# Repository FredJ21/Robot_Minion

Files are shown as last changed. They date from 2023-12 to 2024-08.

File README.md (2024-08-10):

# Le Projet "ROBOT MINION"

***Introduction***

L'objectif de ce projet est de **concevoir** et **réaliser** un petit robot sympa, attractif, mignon, … un **MINION** 🤩 !!  

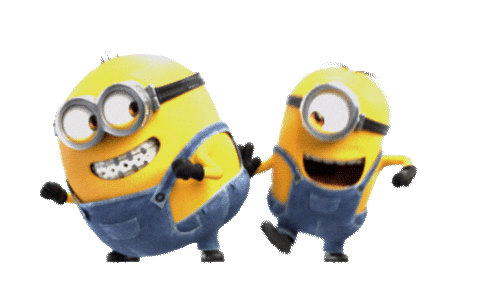
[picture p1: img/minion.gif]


Mais plus globalement, l’objectif de ce projet est de disposer d'**une base robotique** d’étude et de tests, simple, évolutive, et avec bien d'autres caractéristiques et fonctionnalités intéressantes :

* **Robustesse** , **solidité**
   * châssis en fibre de bois médium facile à modifier et réaliser (Découpe Laser). Il pourra également être réalisé en aluminium
   * pièces principales en impression 3D (en PLA ou PETG)

* **Modularité**
   * utilisation de profilés en aluminium 15x15 qui permettent de positionner les plateaux et des accessoires à la hauteur souhaitée
   * matrice de trous pré percés lors de la réalisation du châssis et des plateaux , permettant ainsi de positionner librement les différents éléments et évolutions
   * les pièces 3D disponibles pour éventuellement être modifiées, adaptées  (au format STL & Fusion360)

* **Espace**
   * 54 cm séparent le châssis inférieur et le bas bas du chapeau ,
   * les profilés alu verticaux sont espacés de 150 mm
   * ce qui donne un volume utile intérieur de 15 x 15 x 54 cm , mais certains éléments peuvent être positionnés sur l’extérieur (comme les bras, par exemple)

* **Puissance motrice**
   * motricité par l’utilisation de 2 moteurs CC à fort couple , qui pourront être remplacé par des modèles plus puissant si besoin

* **Programmation** et **connectivité**
   * Une carte Raspberry PI 4 au coeur du robot 🥳 !!! ( pouvant évoluer vers une version 5, bien entendu 😁 )
   * modules USB WiFi ou 4/5G
   * développement en Python (ou autre langage)
   * synthèse et reconnaissance vocal
   * traitement et tracking vidéo , computer vision

* **Evolutions**
   * on pourra greffer à souhait un certain nombre de capteurs, actionneurs, ou autres systèmes électroniques
   * **l’objectif est bien évidemment de faire évoluer** les éléments du robot , bras, tête, motricité …

Le robot, dans cette version, mesure environ 70 cm de haut, le chapeau supérieur et les plateaux ont un diamètre de 250 mm, l'empattement des roues avant/arrière est d’environ 300 mm.

🤔 La ressemblance est toute relative, mais il y a bien un petit aire de famille !!! 😜

<table  width="100%"><tbody>
<tr>
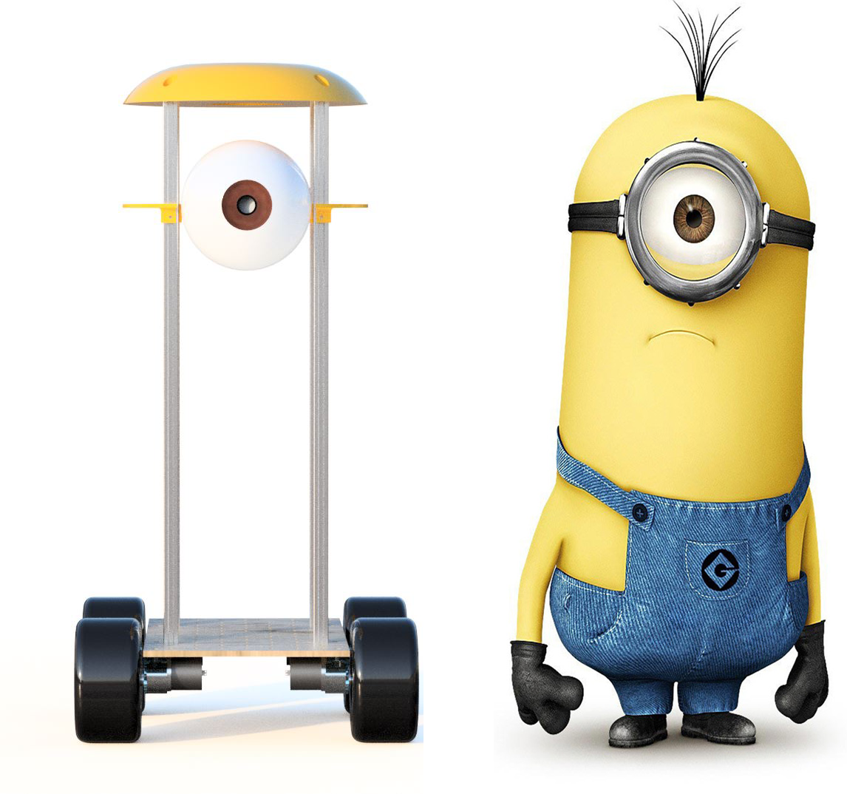
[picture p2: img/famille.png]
<td align="center" width="50%"></td>
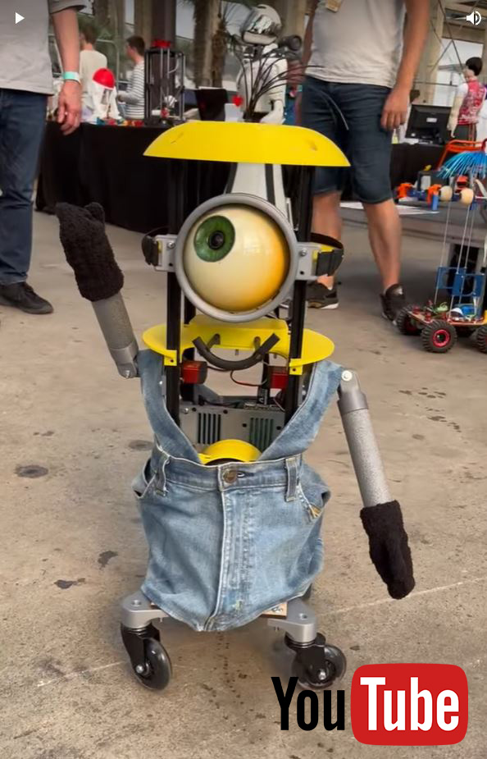
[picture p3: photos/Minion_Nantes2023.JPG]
<td align="center" width="30%">https://youtube.com/shorts/Kb3ByDOdsDA</td>

</tr>
</tbody></table>   

### Sommaire
* Les pièces réalisées en impression 3D
* Les autres pièces
* L'oeil
* La bouche
* Le mécanisme de l'épaule
* Le support de batterie
* L'électronique de commande
* Présentation du projet lors de l'ApéroBot 0x90 - le 11 octobre 2023
* Le projet MINION au JT de France 3 Pays De La Loire

---

## Les pièces réalisées en impression 3D

<table  width="100%"><tbody>
<tr>
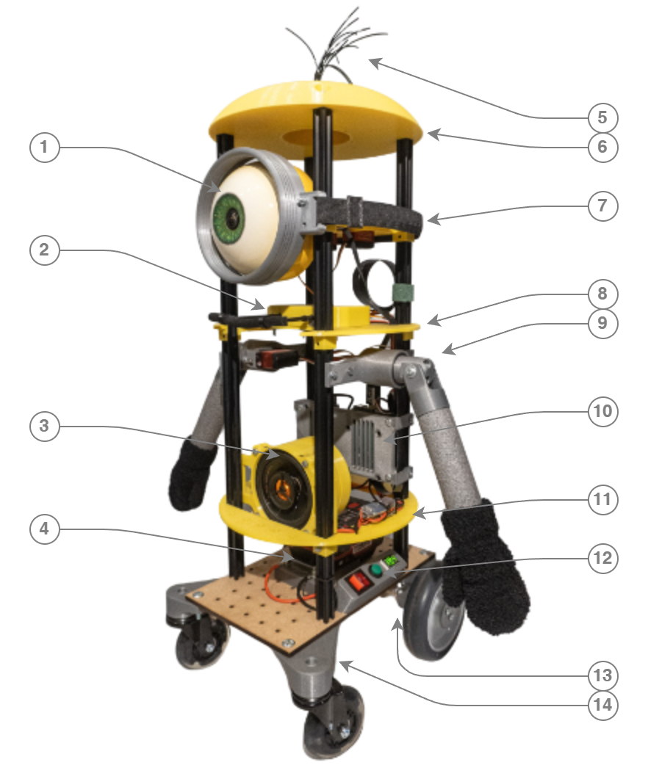
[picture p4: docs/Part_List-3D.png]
   <td width="60%"></td>
   <td align="left">
   (1) - L'<strong>oeil</strong> (voir plus bas) et la <a href="3D_STL/Lunette.stl">lunette</a><br>
   (2) - La <strong>bouche</strong> (voir plus bas)<br>
   (3) - <a href="3D_STL/HP_box.stl">Support du haut parleur</a><br>
   (4) - <strong>Batterie</strong> et sa base d'acceuil (voir plus bas)<br>
   (5) - <strong>Cheveux</strong> avec quelques bouts de TPU<br>
   (6) - <a href="3D_STL/Chapeau.stl">Chapeau</a> & Couvercles<br>
   (7) - <a href="3D_STL/Plateau_oeil_v2.stl">Plateau_oeil</a><br>
   (8) - <a href="3D_STL/Plateau_2.stl">Plateau 2</a><br>
   (9) - L'<strong>épaule</strong> (voir plus bas)<br>
   (10) - <a href="3D_STL/Support_RPI.stl">Support Raspberry PI</a><br>
   (11) - <a href="3D_STL/Plateau_3.stl">Plateau 3</a><br>
   (12) - Boutons de commande sur <a href="3D_STL/Power_button.stl">support</a> <br>
   (13) - <a href="3D_STL/Support_D37.stl">Supports de moteur</a><br>
   (14) - Support de roues libres <a href="3D_STL/Support_Roue_Libre_R.stl">droite</a> et  <a href="3D_STL/Support_Roue_Libre_L.stl">gauche</a><br>
   <br><br>

   </td>
 </tr>
</tbody></table>

- Fichiers STL pour l'impression 3D --> [3D_STL](3D_STL)
- Fichiers sources, au format Fusion 360 --> [3D_Fusion360](3D_Fusion360)

---

## Les autres pièces

<table  width="100%"><tbody>
<tr>
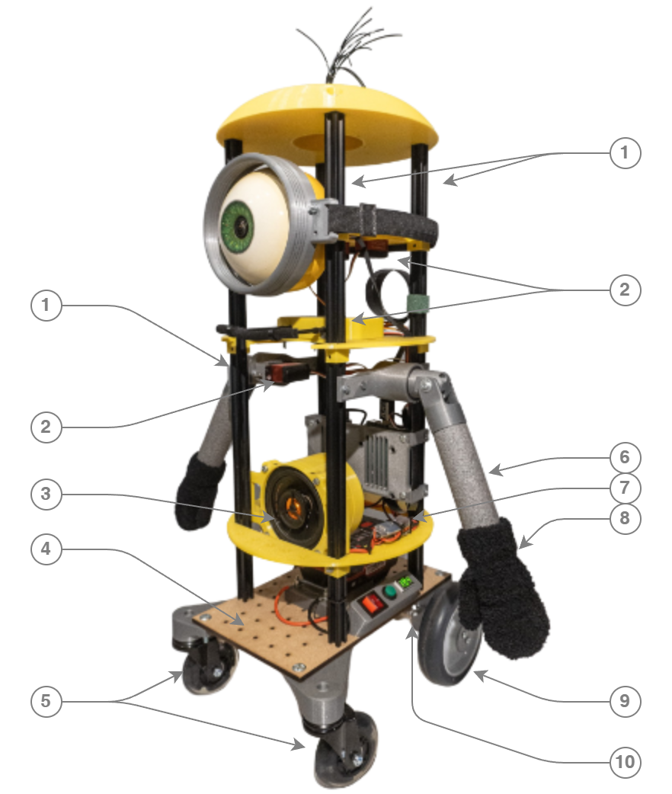
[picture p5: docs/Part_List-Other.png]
   <td width="60%"></td>
   <td align="left">
   (1) - <strong>4 profils</strong> en aluminium anodisé 1515 - 550mm de long <a href="https://fr.aliexpress.com/item/1005004071352633.html">aliexpress.com...</a><br>
   (2) - <strong>Servos moteurs</strong> numériques 30/35Kg.cm 180 degrés <a href="https://fr.aliexpress.com/item/32826867656.html">aliexpress.com...</a> <br>
   (3) - Haut-parleur 20 watts RMS (<a href="https://www.norauto.fr/p/haut-parleurs-norauto-sound-hp-100x-coaxial-2166455.html">norauto.fr...</a>) <br>
   (4) - <strong>Plateau</strong> de bois médium 6mm réalisé en découpe laser <a href="2D/Chassis_v4.svg">fichier svg</a> & dxf <br>
   (5) - <strong>Roulettes</strong> Luminescent Chaise Gamer <a href="https://www.amazon.fr/gp/product/B09N95T18G">amazon.fr...</a><br>
   (6) - <strong>Bras</strong> en mousse (d'isolation thermique en plomberie) diam 35mm <br>
   (7) - <strong>Regulateur</strong> UBEC 7A <a href="https://fr.aliexpress.com/item/32574612952.html">aliexpress.com...</a> <br>
   (8) - Petits gants pour les <strong>mains</strong> <a href="https://www.amazon.fr/gp/product/B0B7MNNZBG">amazon.fr...</a> <br>
   (9) - <strong>Roues</strong> dim 125mm <a href="https://www.leroymerlin.fr/produits/quincaillerie/quincaillerie-du-meuble/roue-et-roulette/roulette-de-meuble/roue-fixe-sur-axe-diam-125-mm-82629474.html">leroymerlin.fr...</a><br>
   (10) - <strong>Moteurs</strong> D37 CC à Brosses 12V 100 RPM 166 oz-in <a href="https://eu.robotshop.com/fr/products/12v-100rpm-166-oz-in-brushed-dc-motor">robotshop.com...</a><br>

   </td>
 </tr>
</tbody></table>

---

## L'oeil

L'oeil est réalisé en impression 3D avec poncage, peinture, et protection à la résine époxy. <br>
Il est articulé en X et Y autour d'un axe monté sur roulement.<br>
Il embarque une camera pour la carte Raspberry PI

***L'oeil est composé de plusieurs pièces :***

- la sphere de diamètre 130mm - <a href="3D_STL/Oeil_130.stl">Oeil_130.stl</a>
- un support pour la caméra - <a href="3D_STL/Oeil_Support_Cam.stl">Oeil_Support_Cam.stl</a>
- le support de l'oeil - <a href="3D_STL/Oeil_Support.stl">Oeil_Support.stl</a>
- l'axe - <a href="3D_STL/Oeil_Axe.stl">Oeil_Axe.stl</a>
- le raccordement au plateau - <a href="3D_STL/Oeil_Raccord_Plateau.stl">Oeil_Raccord_Plateau.stl</a>

<br>

- 3 roulements 608ZZ 8x22x7 <a href="https://www.amazon.fr/Roulements-Bearings-Skateboard-Longboard-Waveboard/dp/B07S3SZZST">amazon.fr...</a> <br>
- une camera RPI grand angle 175° <a href="https://fr.aliexpress.com/item/32881466491.html">aliexpress.com...</a> <br>
- <strong>2 Servos moteurs</strong> numériques 30/35Kg.cm 180 degrés <a href="https://fr.aliexpress.com/item/32826867656.html">aliexpress.com...</a> <br>

<table width="100%">
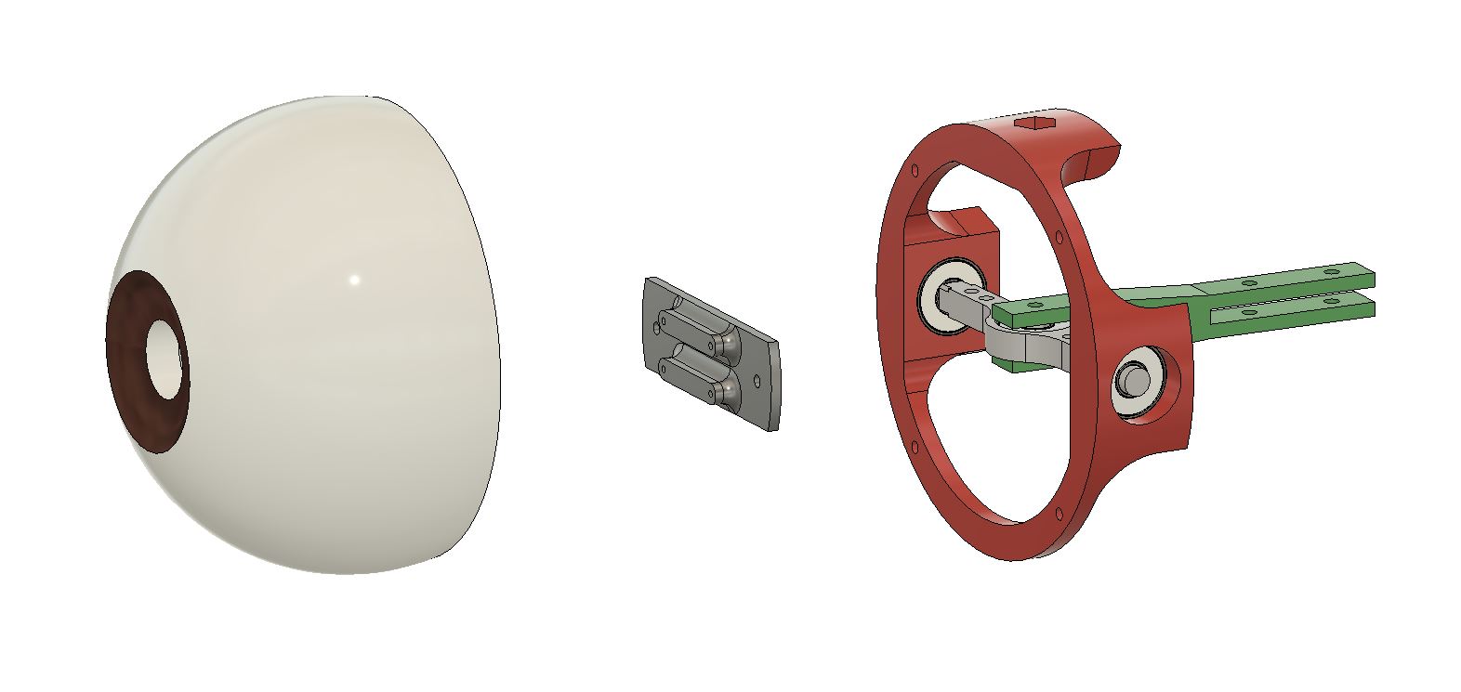
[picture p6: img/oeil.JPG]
<td align="center"></td>
</table>

- Piéces imprimées --> [3D_STL](3D_STL)
- Fichiers sources, au format Fusion 360 --> [3D_Fusion360](3D_Fusion360)

---
## La bouche

La bouche est réalisée avec 2 servos moteurs, quelques pièces imprimées, et un petit "boudin" de silicone

- Piéces imprimées
  - support pour les 2 moteurs --> [Bouche_1.stl](3D_STL/Bouche_1.stl)
  - 2 tiges --> [Bouche_2.stl](3D_STL/Bouche_2.stl)
  - le couvercle --> [Bouche_Couvercle.stl](Bouche_Couvercle.stl)
- Fichiers sources, au format Fusion 360 --> [3D_Fusion360](3D_Fusion360)

<table width="100%">
<td align="center">
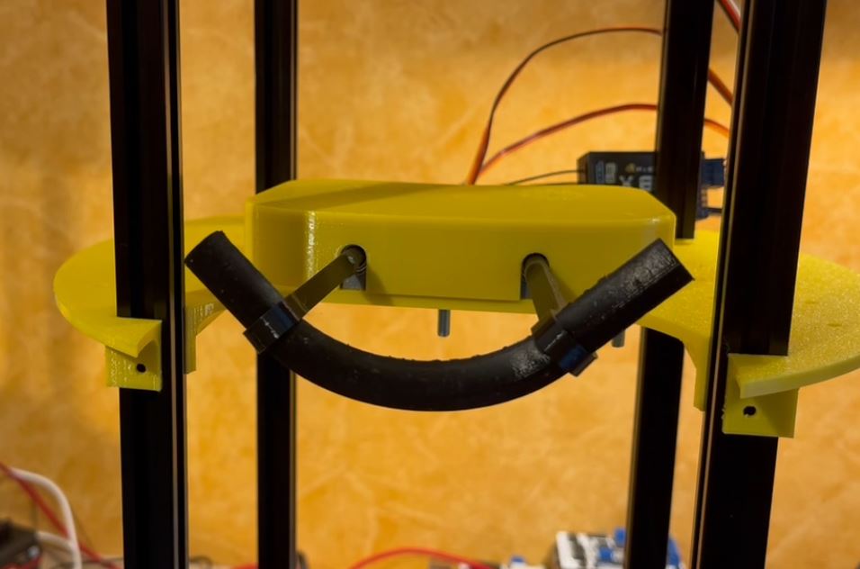
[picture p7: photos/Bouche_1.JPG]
 -
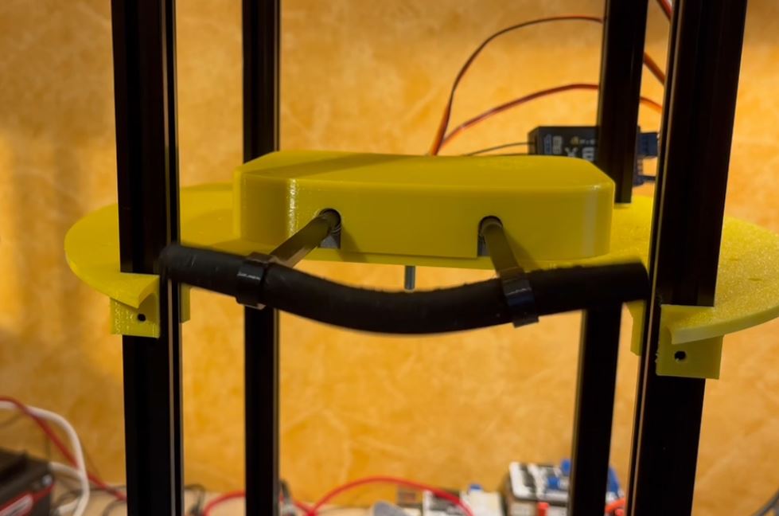
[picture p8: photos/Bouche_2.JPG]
 -
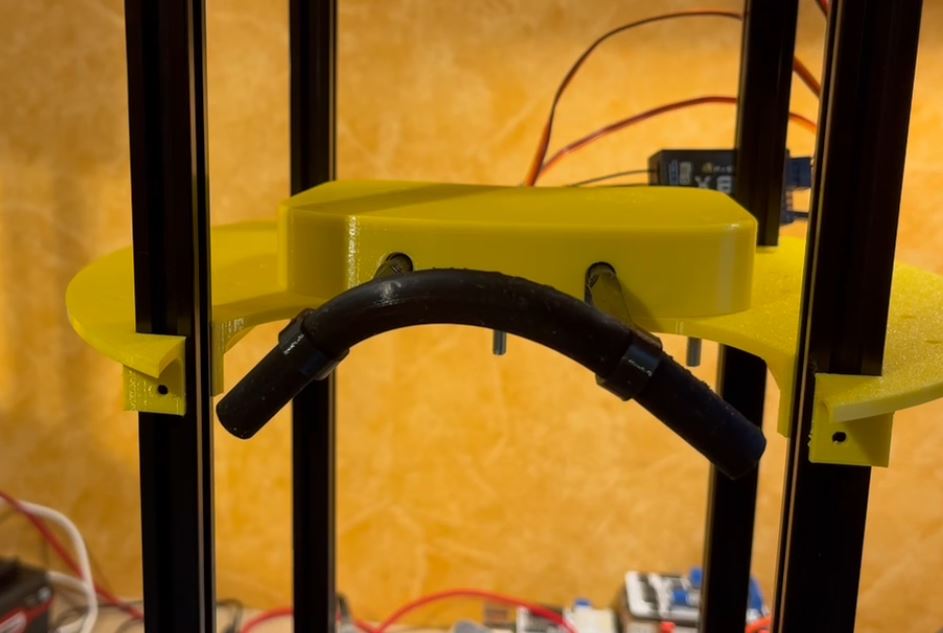
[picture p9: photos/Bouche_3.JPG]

</td>
</table>

---
## Le mécanisme de l'épaule

L'épaule est réalisée en impression 3D avec un servo moteur 30/35Kg et 2 roulements

- <strong>Servos moteurs</strong> numériques 30/35Kg.cm 180 degrés <a href="https://fr.aliexpress.com/item/32826867656.html">aliexpress.com...</a> <br>
- <strong>Roulements</strong> 30x37x4mm  <a href="https://www.amazon.fr/gp/product/B09SCMJTPJ/ref=ppx_yo_dt_b_search_asin_title">amazon.fr...</a> <br>
- 3 piéces imprimées --> [3D_STL](3D_STL)
- Fichiers sources, au format Fusion 360 --> [3D_Fusion360](3D_Fusion360)

<table width="100%">
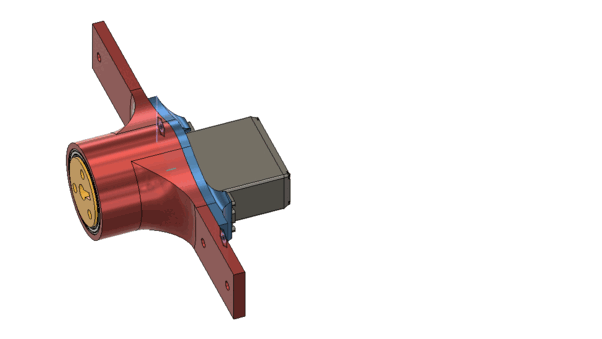
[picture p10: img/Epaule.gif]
<tr> <td align="center"> </td> </tr>
</table>

---

## Le support de batterie
***Liens & info*** :
- Batterie Parkside PAP 20 B3 - 20 V 4000mAh 80wh
- Chargeur Parkside PLG 20 C3
- petites lamelles en cuivre étamées ( réalisé avec un vieux tube de cuivre de plomberie )
- quelques vis M4

***Fichiers 3D*** :
- [Support_Batterie_up.stl](3D_STL/Support_Batterie_up.stl)
- [Support_Batterie_down.stl](3D_STL/Support_Batterie_down.stl)
- source : [Support_Batterie_Parkside.f3d](3D_Fusion360/)

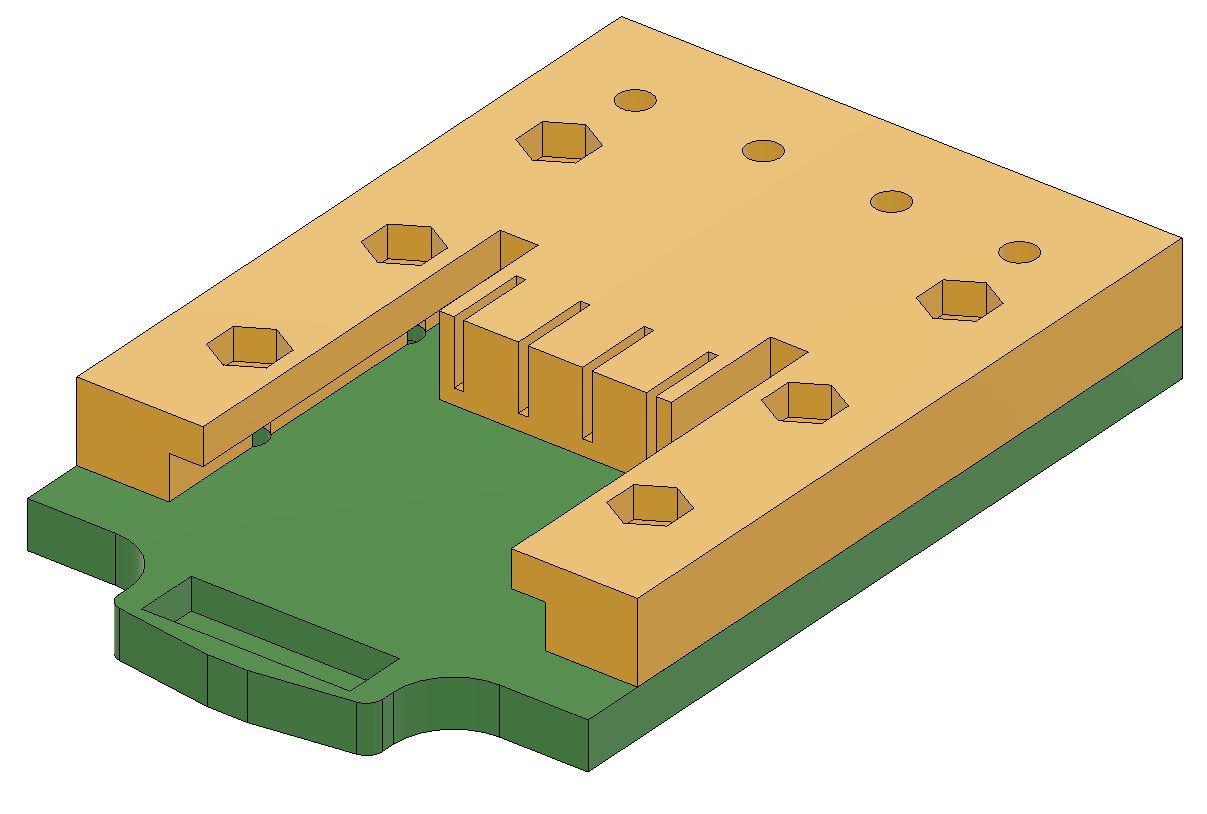
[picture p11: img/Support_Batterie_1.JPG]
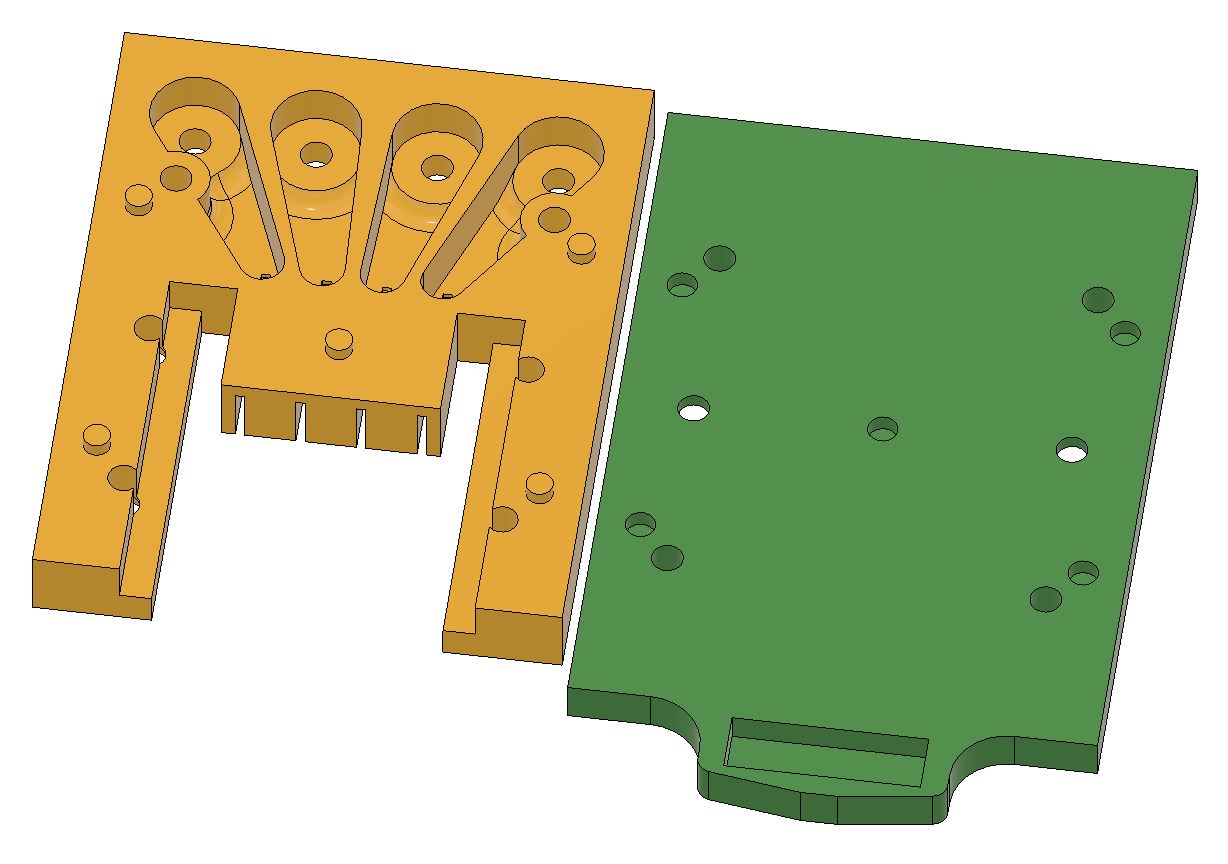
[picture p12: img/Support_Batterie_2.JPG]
| ||
|-----|-----|

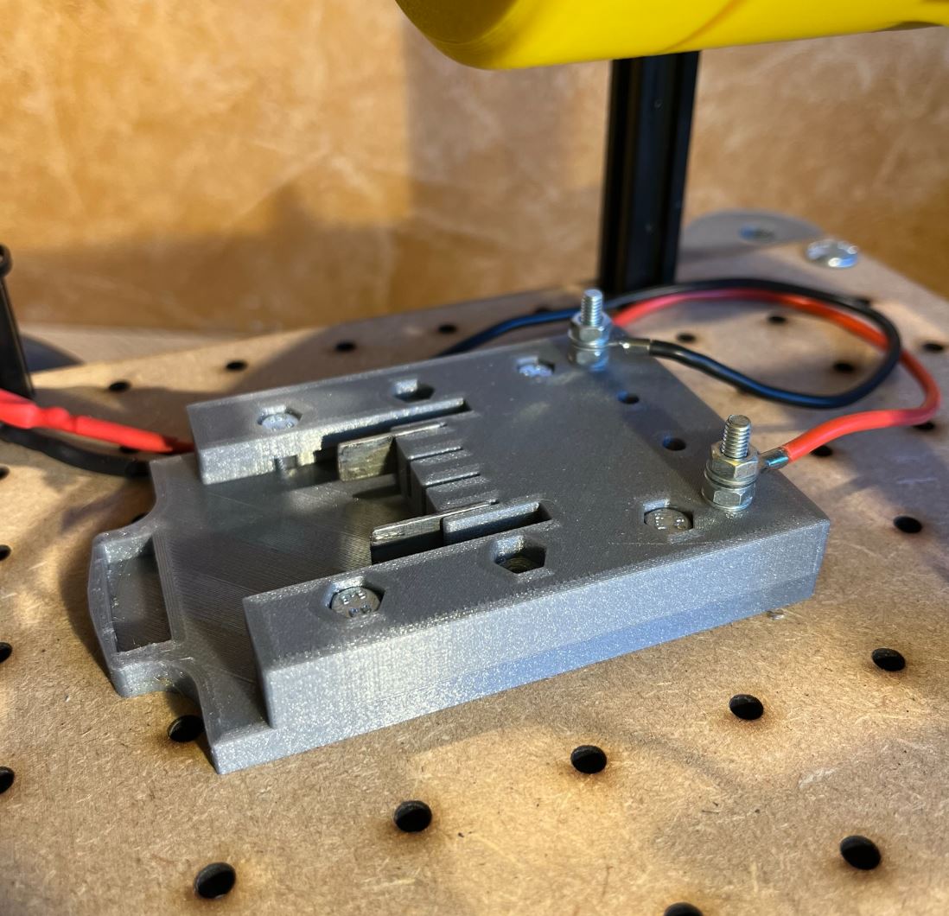
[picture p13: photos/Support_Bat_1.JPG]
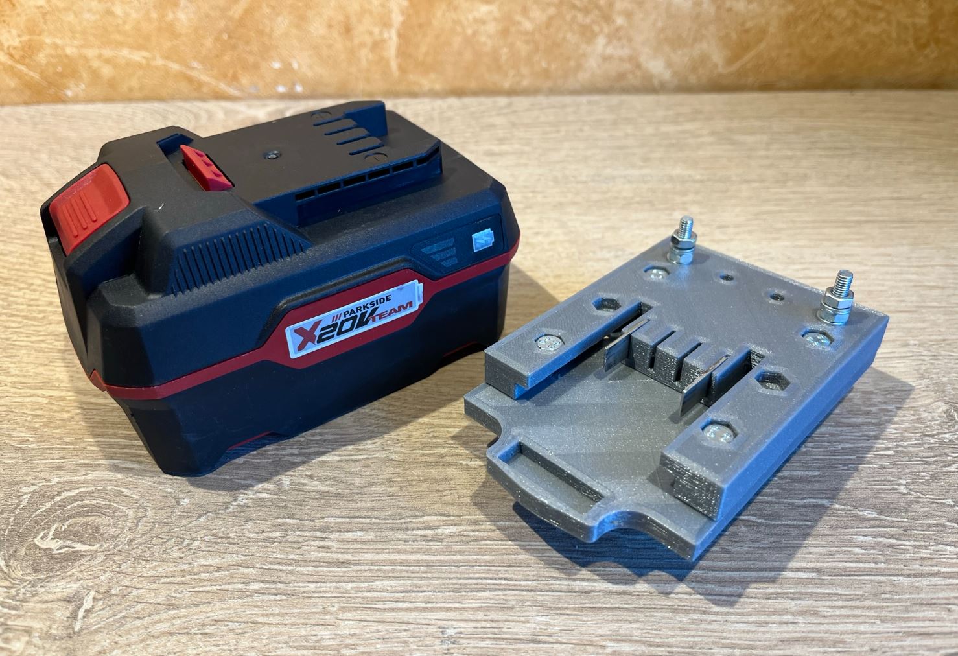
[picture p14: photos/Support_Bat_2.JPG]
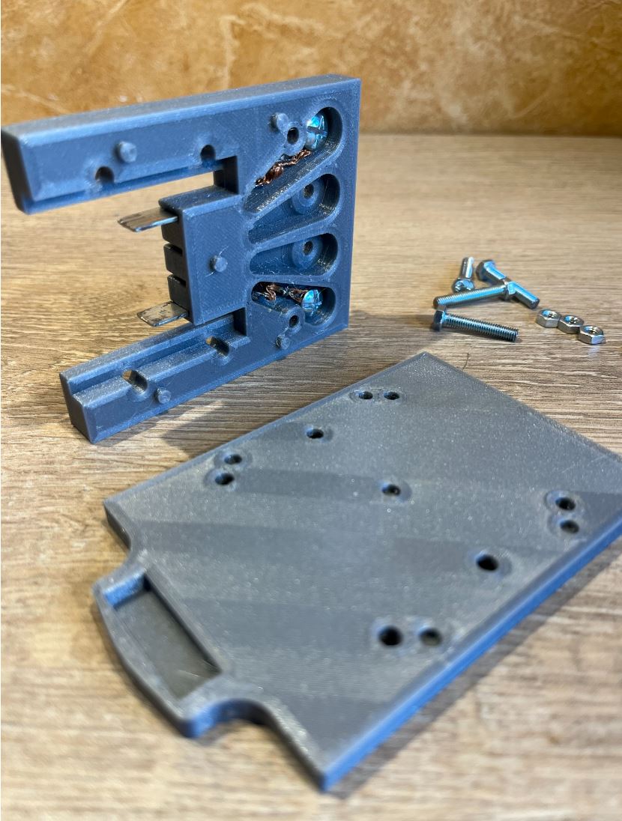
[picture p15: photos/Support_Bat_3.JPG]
|  |  |  |
|-----|-----|-----|

---

## L'électronique de commande

L'électronique embarquée est composée principalement :
- d'une carte Raspberry PI équipée d'une carte d'extension(*) (un HAT) pour la commande moteur https://github.com/FredJ21/Raspberry_PI_MotorDriverHat#readme
- d'un amplificateur audio
- d'un module WiFi USB
- de 2 regulateurs 5V afin séparer l'alimentation du RPI et des servos moteurs

***Important :*** Le projet peut également être réalisé sans cette carte d'extension "maison". Il suffira juste de choisir des drivers moteurs adaptés

<table  width="100%"><tbody>
<tr>
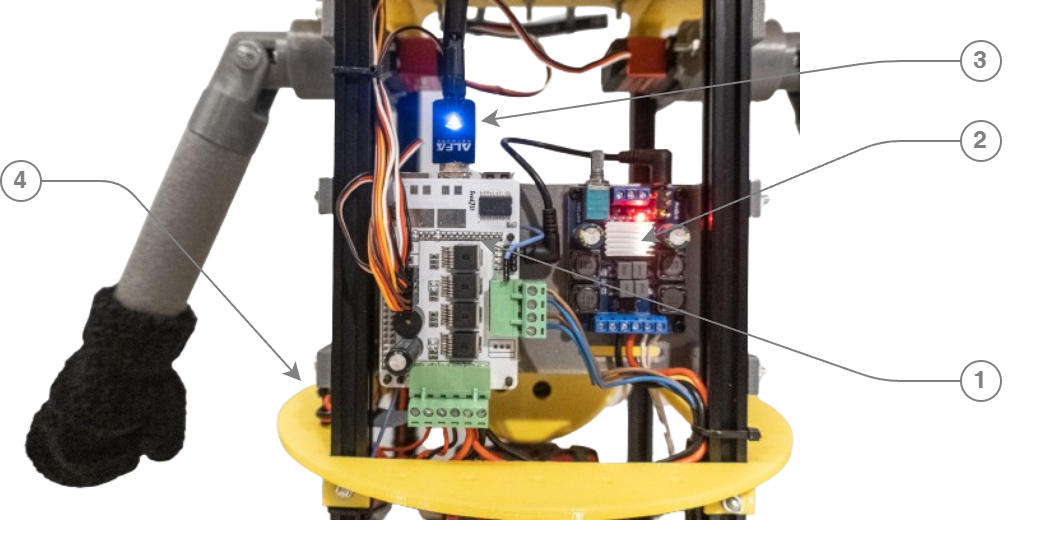
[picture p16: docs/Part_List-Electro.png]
   <td width="60%"></td>
   <td align="left">
   (1) - Une carte <strong>Raspberry PI</strong> 4 (ou 5 ! ) <a href="https://www.kubii.com/">www.kubii.com...</a><br>
   (2) - Une carte d'amplificateur numérique <a href="https://www.amazon.fr/gp/product/B09PL6R1L7">amazon.fr...</a> <br>
   (3) - Une carte WiFi USB (<a href="https://www.amazon.fr/gp/product/B0752CTSGD">amazon.fr...</a>) <br>
   (4) - <strong>2 Régulateurs</strong> UBEC 7A <a href="https://fr.aliexpress.com/item/32574612952.html">aliexpress.com...</a> <br>

   </td>
 </tr>
</tbody></table>

***Schéma global***

Schéma de principe avec la carte Raspberry PI, la carte d'extension (HAT drivers moteurs), et les éléments périphériques.

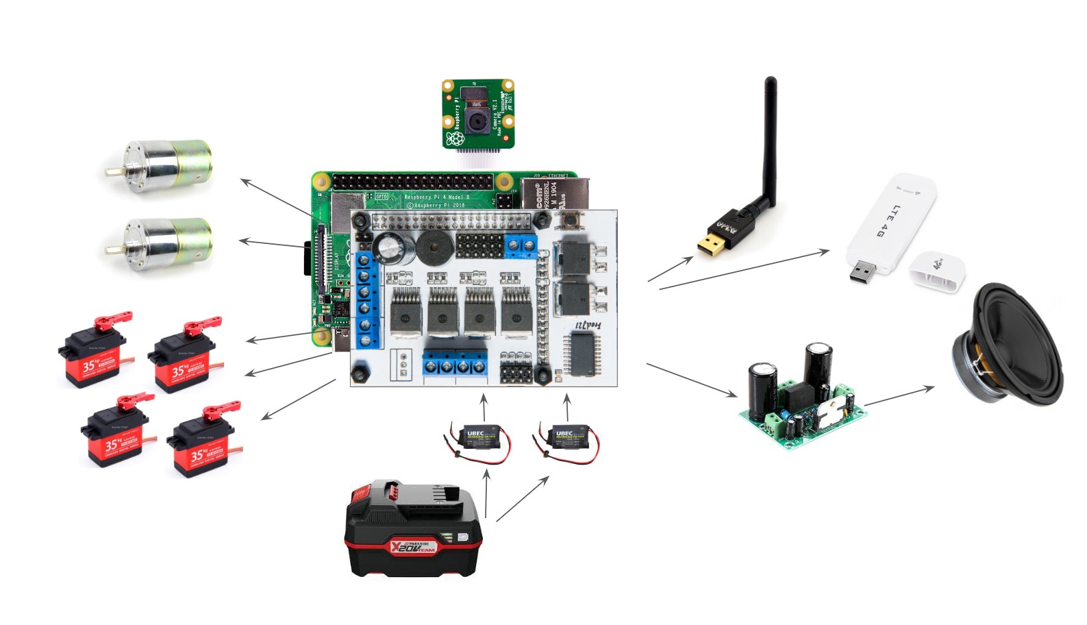
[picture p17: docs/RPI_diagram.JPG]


***Schéma de raccordement***

La carte d'extention permet de raccorder 3 alimentations distinctes :
- la tension directe de la batterie ~ 20V , pour l'alimentation des moteurs
- une tention régulée de 5V pour les servos moteurs
- une tention régulée de 5V pour la carte Raspberry PI

Les 2 moteurs CC ( pour le déplacement du robot ) sont raccordées à la carte d'extention
- GPIO 24 & 25 --> Mosfets moteur droit
- GPIO 26 & 27 --> Mosfets moteur gauche

Les servos moteurs sont raccordés aux sorties :
- GPIO 5 --> Oeil X
- GPIO 6 --> Oeil Y
- GPIO 12 --> Bras Droit
- GPIO 13 --> Bras Gauche
- GPIO 7 --> Bouche moteur Droit
- GPIO 8 --> Bouche moteur Gauche

De plus, la carte dispose d'autres GPIO libres , et de :
- GPIO 18 --> buzzer
- GPIO 19 --> Bouton poussoir

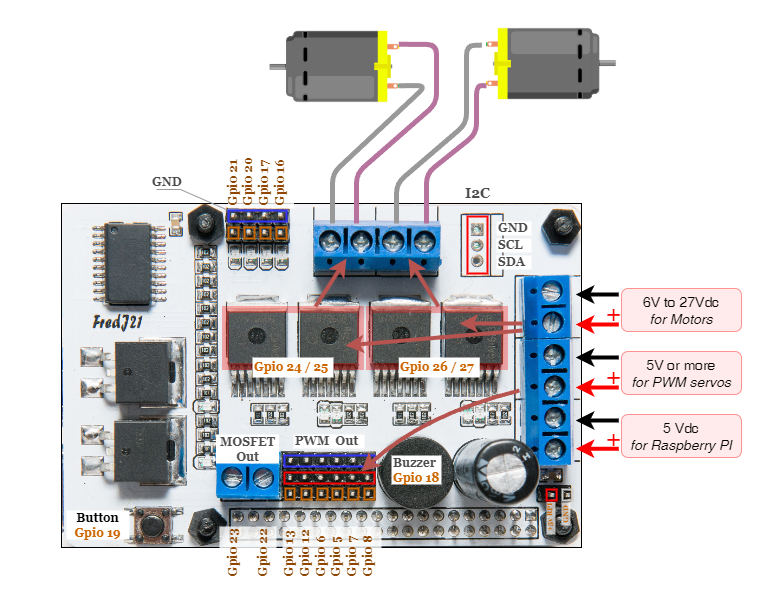
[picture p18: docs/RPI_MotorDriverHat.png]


***Raspberry PI - PinOut***

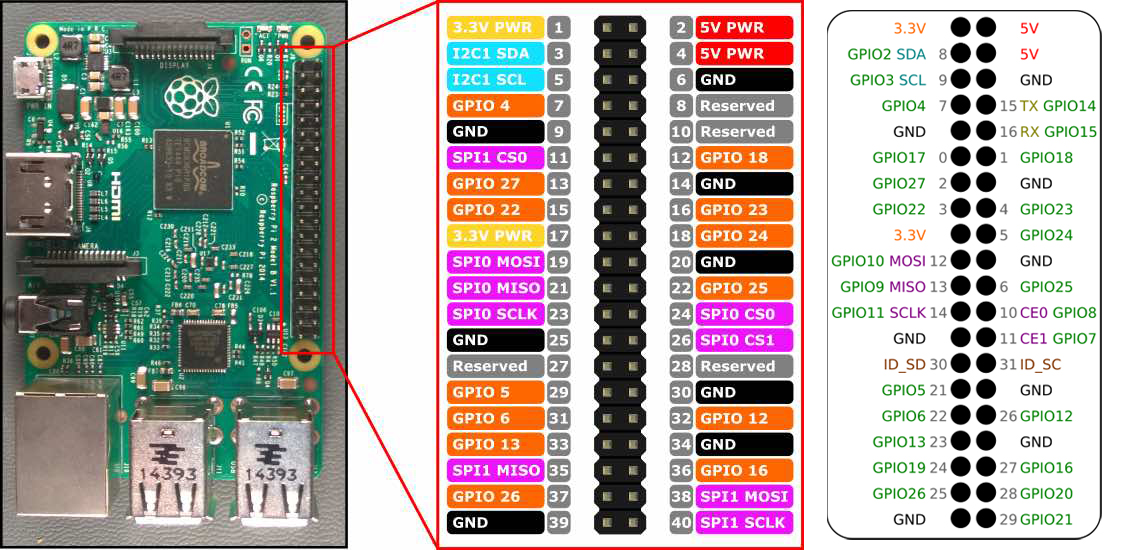
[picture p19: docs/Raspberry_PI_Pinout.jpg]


---

## Programmation

Le programme de gestion et son interface Web sont toujours en cours de développement ...
... mais je tente de stabliser et simplifier l'installation, ainsi que le packaging .... dans en autre Repos Git  :
( actuellement en cours de construction ) 

https://github.com/FredJ21/Robot_Minion_Dev

---

## Présentation du projet lors de l'ApéroBot 0x90 - le 11 octobre 2023
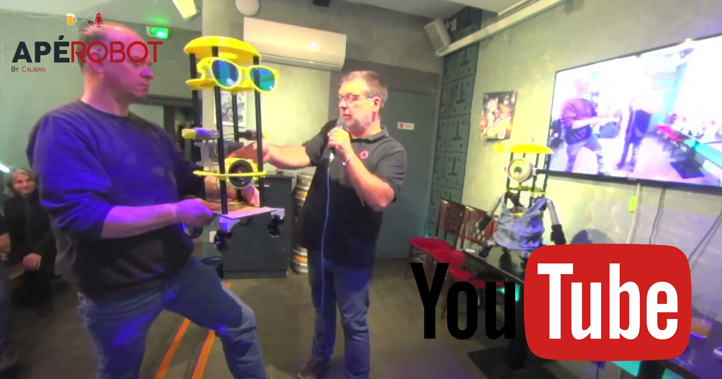
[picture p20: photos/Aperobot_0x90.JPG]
<br>
- https://youtu.be/tXXc-RWyAaM
- Slides de présentation: [202310_Caliban_Robot_MINION.pptx](https://docs.google.com/presentation/d/1i7fHR1yLxM-sZlLi-bkuZh3kFmp7REDd2zA3NFKi7cQ/)

---

## Le projet MINION au JT de France 3 Pays De La Loire
- JT du 7 Juillet 2023 - Nantes Maker Campus 2023

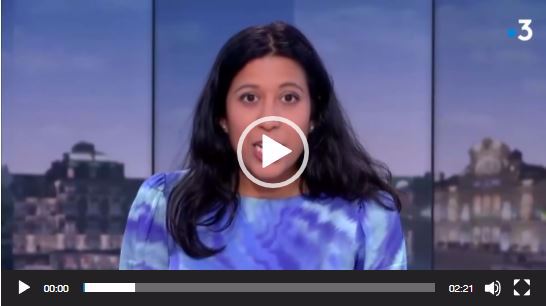
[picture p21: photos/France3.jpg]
<br>
- https://youtu.be/sHJWs27naQQ

---

### Authors
Frederic JELMONI<br>
https://www.youtube.com/@fred-robotic<br>
https://www.facebook.com/fredrobotic<br>

### MIT License
Permission is hereby granted, free of charge, to any person obtaining a copy
of this software and associated documentation files (the "Software"), to deal
in the Software without restriction, including without limitation the rights
to use, copy, modify, merge, publish, distribute, sublicense, and/or sell
copies of the Software, and to permit persons to whom the Software is
furnished to do so, subject to the following conditions:

The above copyright notice and this permission notice shall be included in all
copies or substantial portions of the Software.

THE SOFTWARE IS PROVIDED "AS IS", WITHOUT WARRANTY OF ANY KIND, EXPRESS OR
IMPLIED, INCLUDING BUT NOT LIMITED TO THE WARRANTIES OF MERCHANTABILITY,
FITNESS FOR A PARTICULAR PURPOSE AND NONINFRINGEMENT. IN NO EVENT SHALL THE
AUTHORS OR COPYRIGHT HOLDERS BE LIABLE FOR ANY CLAIM, DAMAGES OR OTHER
LIABILITY, WHETHER IN AN ACTION OF CONTRACT, TORT OR OTHERWISE, ARISING FROM,
OUT OF OR IN CONNECTION WITH THE SOFTWARE OR THE USE OR OTHER DEALINGS IN THE
SOFTWARE.

### Copyright
Copyright (c) 2023 Frederic JELMONI

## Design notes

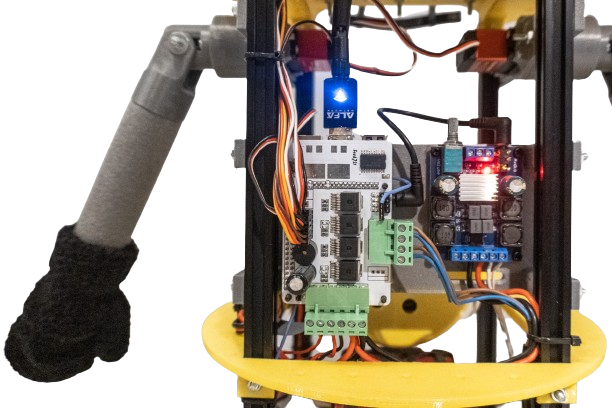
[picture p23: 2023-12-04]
docs/2023-12_Minion_2.png

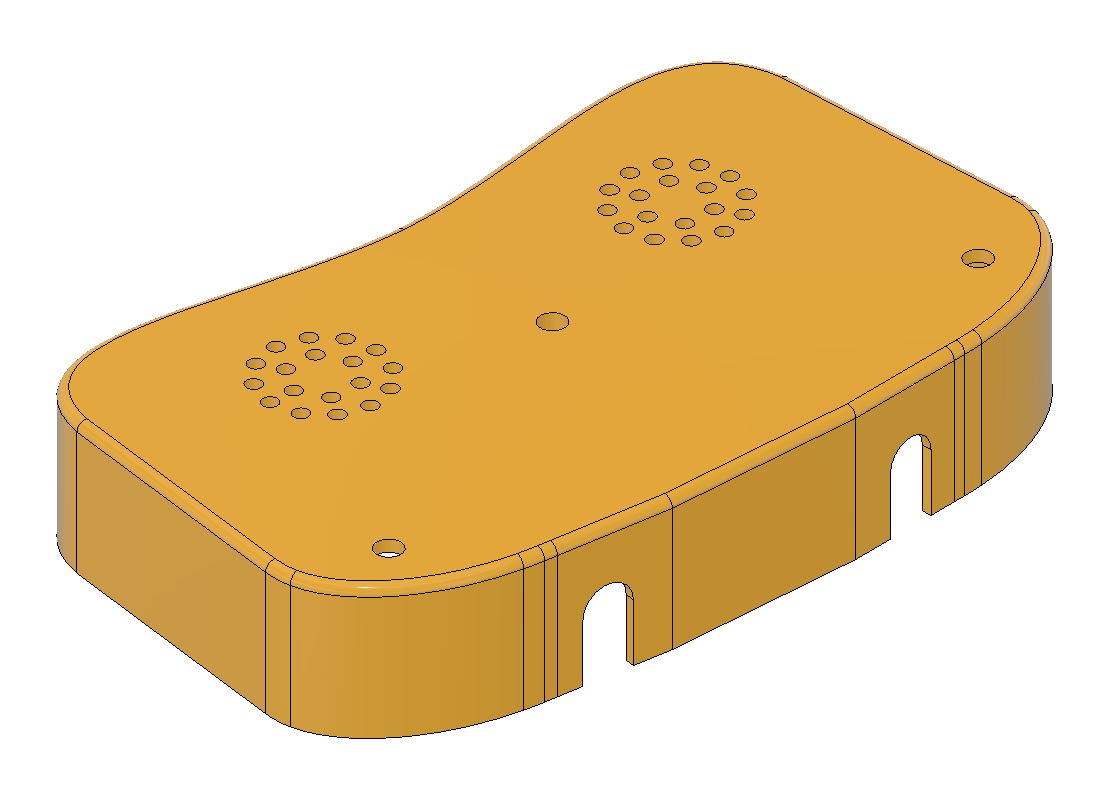
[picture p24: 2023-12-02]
img/bouche_couvercle.jpg

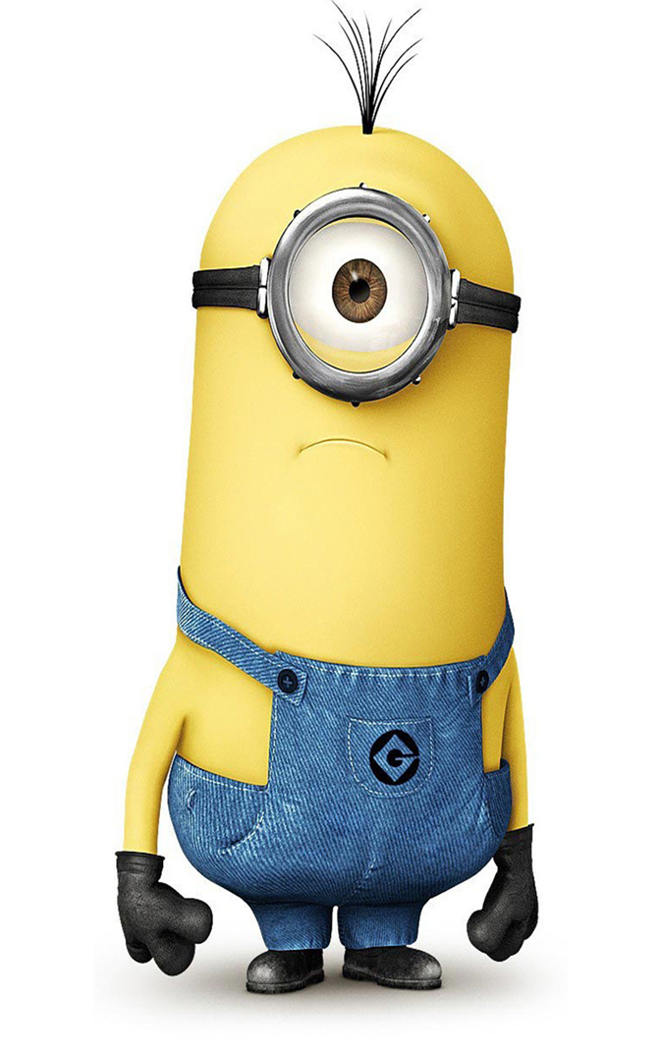
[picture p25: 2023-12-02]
img/mignon2.png

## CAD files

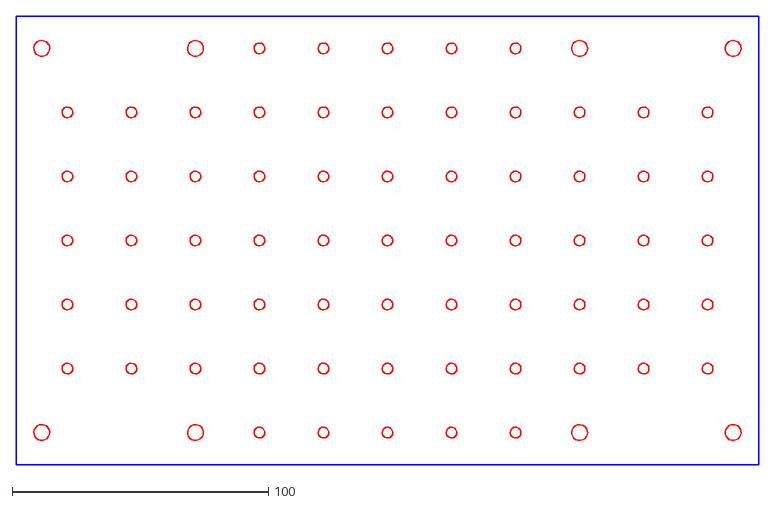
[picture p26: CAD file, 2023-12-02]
2D/Chassis_v4.dxf
290.0 x 175.0

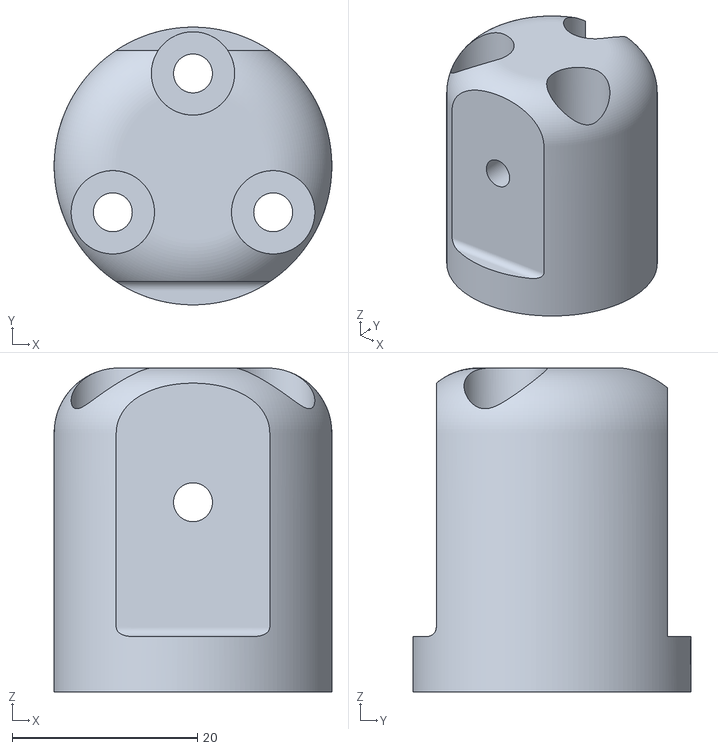
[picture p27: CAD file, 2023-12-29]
3D_STL/Epaule_4.stl
30.0 x 30.0 x 35.0

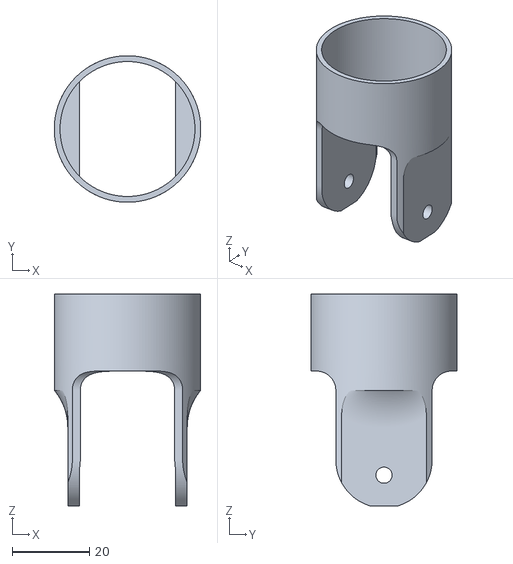
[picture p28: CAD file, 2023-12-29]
3D_STL/Epaule_5.stl
38.0 x 38.0 x 55.0

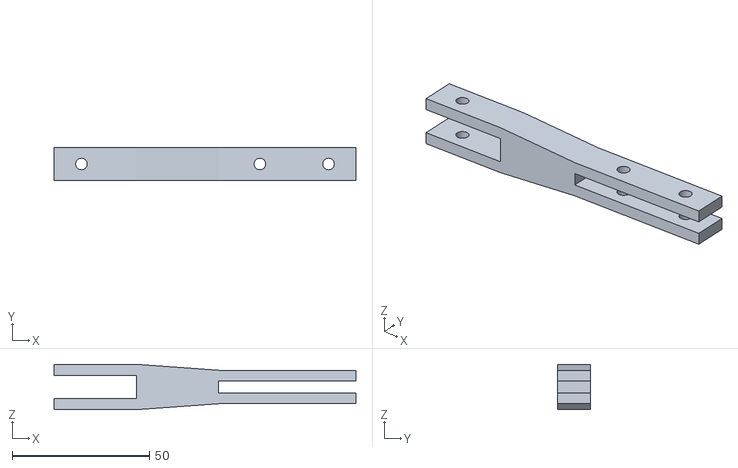
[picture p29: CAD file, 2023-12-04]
3D_STL/Oeil_Raccord_Plateau.stl
110.0 x 12.0 x 16.5

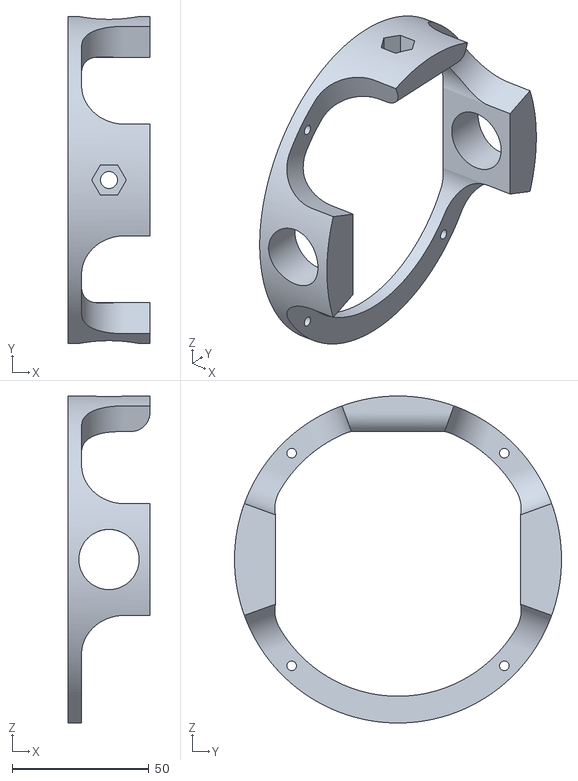
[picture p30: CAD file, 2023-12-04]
3D_STL/Oeil_Support.stl
30.0 x 119.6 x 119.6

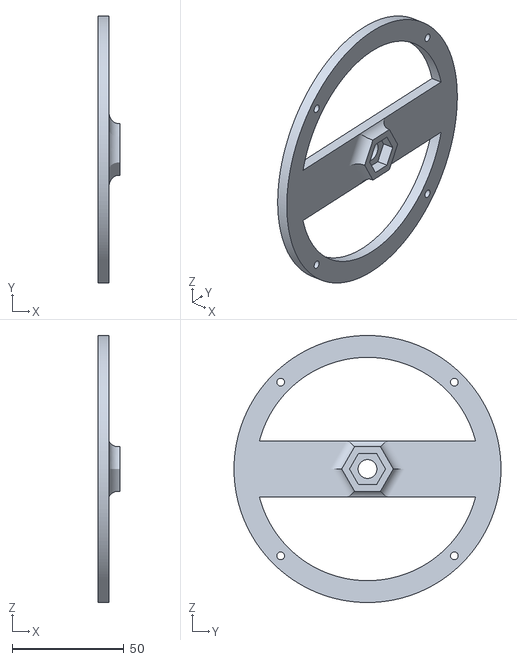
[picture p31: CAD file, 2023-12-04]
3D_STL/Oeil_Support_pour_peinture.stl
10.0 x 119.6 x 119.6

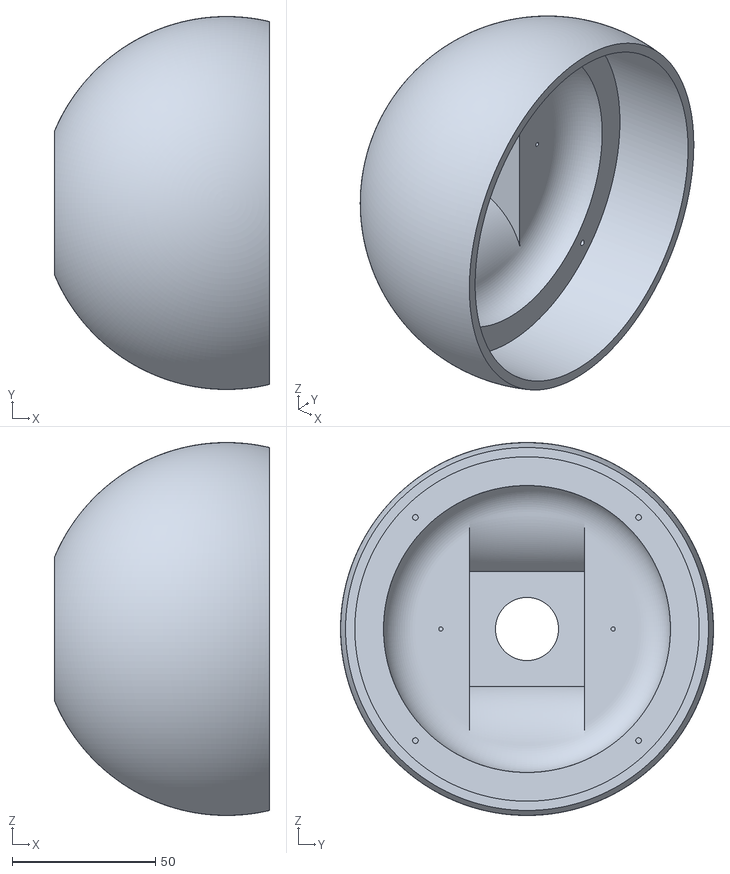
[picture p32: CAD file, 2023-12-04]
3D_STL/Oeil_130.stl
75.0 x 130.0 x 130.0

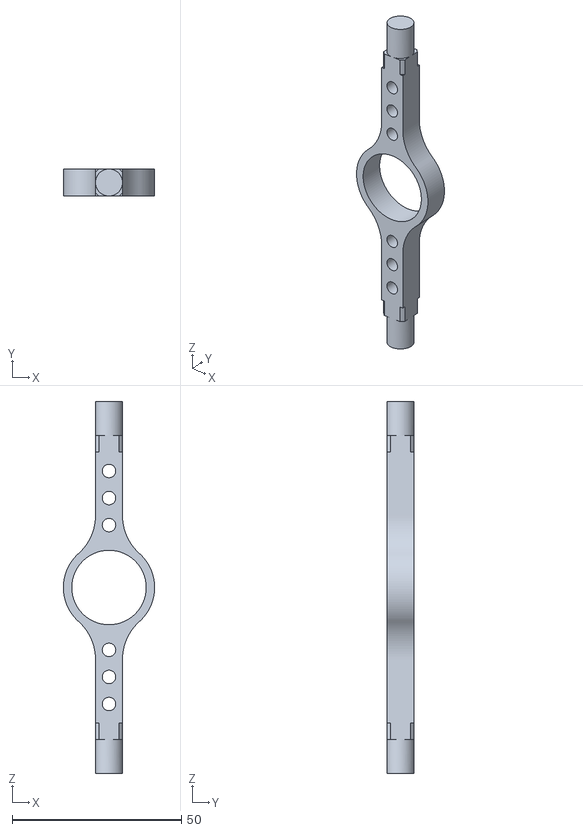
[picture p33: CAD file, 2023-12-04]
3D_STL/Oeil_Axe.stl
27.0 x 8.00 x 110.0

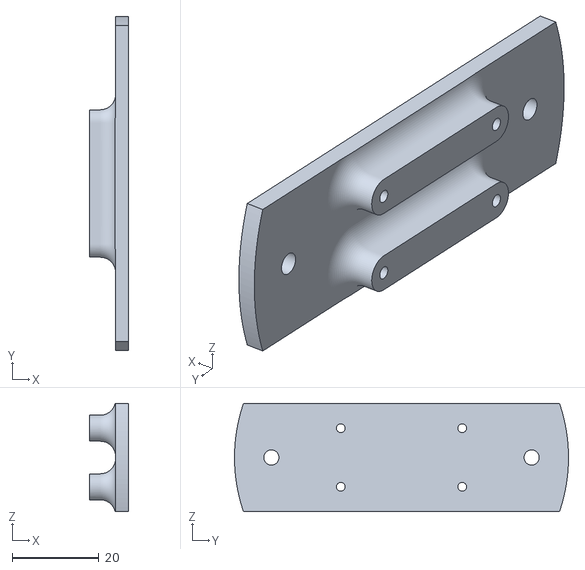
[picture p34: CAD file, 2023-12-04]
3D_STL/Oeil_Support_Cam.stl
9.00 x 77.0 x 25.0

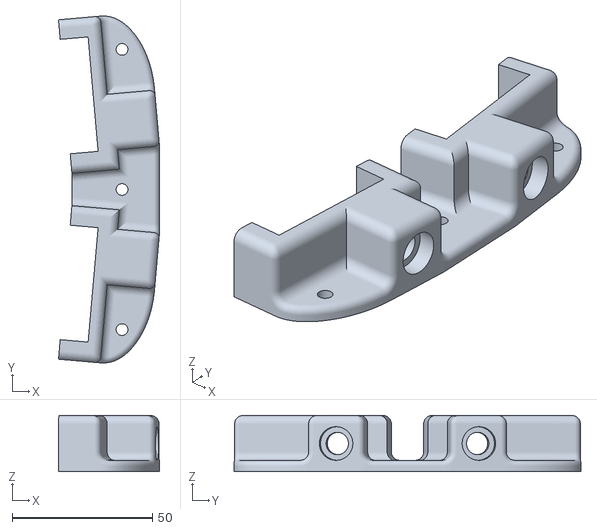
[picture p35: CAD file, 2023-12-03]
3D_STL/Bouche_1.stl
36.1 x 123.8 x 20.0

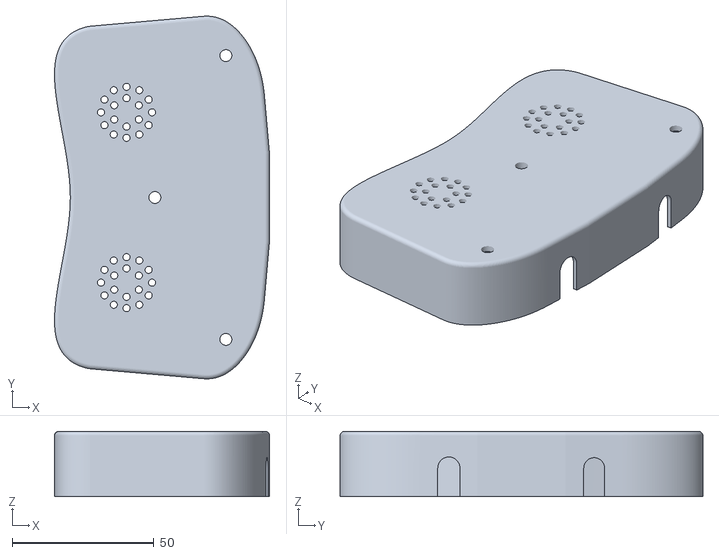
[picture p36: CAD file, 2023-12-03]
3D_STL/Bouche_Couvercle.stl
75.8 x 127.8 x 23.0

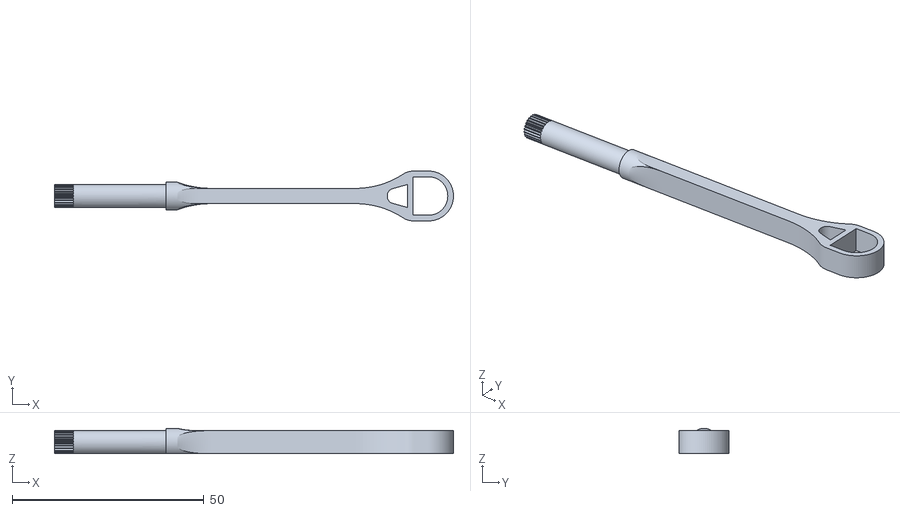
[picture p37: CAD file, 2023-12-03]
3D_STL/Bouche_2.stl
104.0 x 13.0 x 6.61

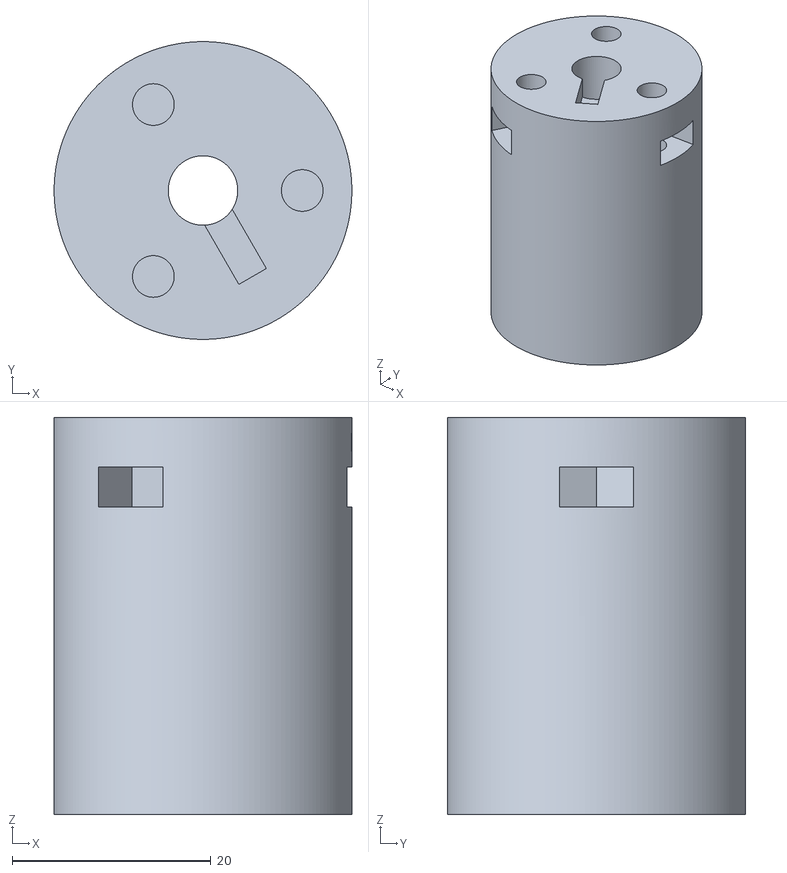
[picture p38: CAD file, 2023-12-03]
3D_STL/Epaule_2.stl
30.0 x 30.0 x 40.0

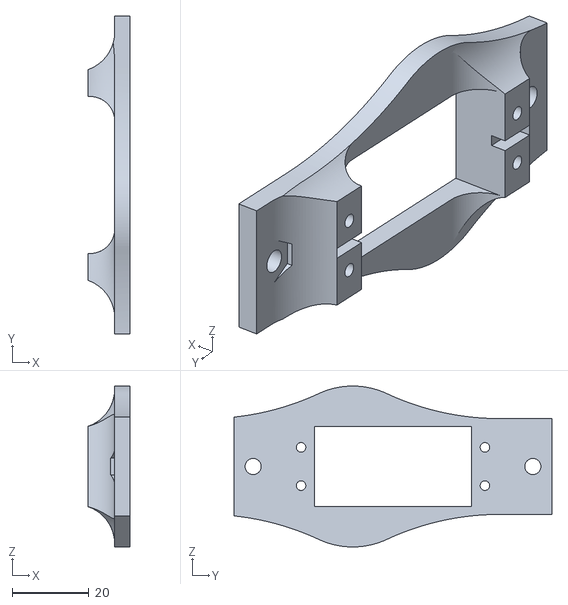
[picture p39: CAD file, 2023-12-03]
3D_STL/Epaule_3.stl
11.0 x 83.0 x 42.0

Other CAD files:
3D_STL/Epaule_1.stl
3D_STL/Support_RPI.stl
3D_STL/Support_RPI_part.stl
3D_STL/HP_Arriere.stl
3D_Fusion360/Bouche.f3z
3D_Fusion360/Chapeau.f3d
3D_Fusion360/Epaule.f3z
3D_Fusion360/Epaule_4.f3d
3D_Fusion360/Epaule_5.f3d
3D_Fusion360/Lunette.f3d
3D_Fusion360/Lunette_double.f3d
3D_Fusion360/Moteur D37.f3d
3D_Fusion360/Oeil_130.f3z
3D_Fusion360/Plateau_1.f3d
3D_Fusion360/Plateau_2.f3d
3D_Fusion360/Plateau_3.f3d
3D_Fusion360/Plateau_oeil_v1.f3d
3D_Fusion360/Plateau_oeil_v2.f3d
3D_Fusion360/Power_button.f3d
3D_Fusion360/Roue.f3d
3D_Fusion360/Roue_Folle.f3d
3D_Fusion360/Support HP.f3d
3D_Fusion360/Support_Batterie_Parkside.f3d
3D_Fusion360/Support_Moteur.f3d
3D_Fusion360/Support_RPI.f3d
3D_Fusion360/Support_roue_libre.f3d
3D_STL/Chapeau.stl
3D_STL/Couvercle_1.stl
3D_STL/Couvercle_2.stl
3D_STL/HP_Avant.stl
3D_STL/HP_Box.stl
3D_STL/Lunette.stl
3D_STL/Lunette_double.stl
3D_STL/Plateau_1.stl
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

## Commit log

2023-12-02 Add init directory
    [Chassis_v4.dxf]
2023-12-02 add 3D files
    [Support_Batterie_Parkside.f3d, Support_Batterie_down.stl, Support_Batterie_up.stl]
2023-12-03 Add chapeau.stl
    [Chapeau.f3d, Chapeau.stl, Couvercle_1.stl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]
2023-12-03 add epaule
    [Epaule.f3z, Epaule_1.stl, Epaule_2.stl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]
2023-12-04 add Oeil
    [Eyes 130.f3z, Oeil_130.stl, Oeil_Axe.stl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]
2023-12-05 Add stl
    [Lunette.stl, Oeil_130.f3z]
2023-12-29 add Epaule 4 & 5
    [Epaule_5.f3d, Epaule_5.stl, epaule_4.f3d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]
2023-12-29 add MotorDriverHat schema
